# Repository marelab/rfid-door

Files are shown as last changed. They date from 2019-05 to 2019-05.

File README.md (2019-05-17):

marelab rfid-door
# ESP8266 RFID - Access Control with Wiegand Protocol powerd by Door Bell transformer 8-12V AC or DC

## First of all 
big thanks to the [ESP-RFID Project](https://github.com/esprfid/esp-rfid) with the work they have done. The "rfid-door" hardware is 100% compatible with their software also a modified [Firmware](https://github.com/marelab/esp-rfid/releases) with extended MQTT support is included with the marelab RFID-DOOR Version that can be used. Just the hardware design is differnt in my version. The RFID-DOOR pcb is designed to be powered directly from the AC Ring Bell transformer (8-12V AC). But can also be configured to use a 8-12V DC power by just solder bridges. Main reason why I used a different design was the fact that I didn't wanted to setup a new DC source and cables for that device, it can be integrated without any extra power infrastructure. Most german households have a AC Ringbell with 8 or 12V transformer next to the door. 

## RFID-DOOR
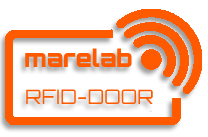
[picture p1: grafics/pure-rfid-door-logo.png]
 
 NFC/RFID WIFI Access Control hardware interfacing a cheap MFRC522, PN532 RFID, RDM6300 readers or Wiegand RFID readers with a Espressif's ESP8266 Microcontroller as Wifi Bridge to drive the door open coil to unlock a home door and to include it into a home automatisation system. The pcb is designed with [KiCad](http://kicad-pcb.org/) an opensoure EDA System. Ready Gerber Files can be found under Gerber. Plz use the Version Tab for download the newest Release the Master Branch includes the current development stage! 

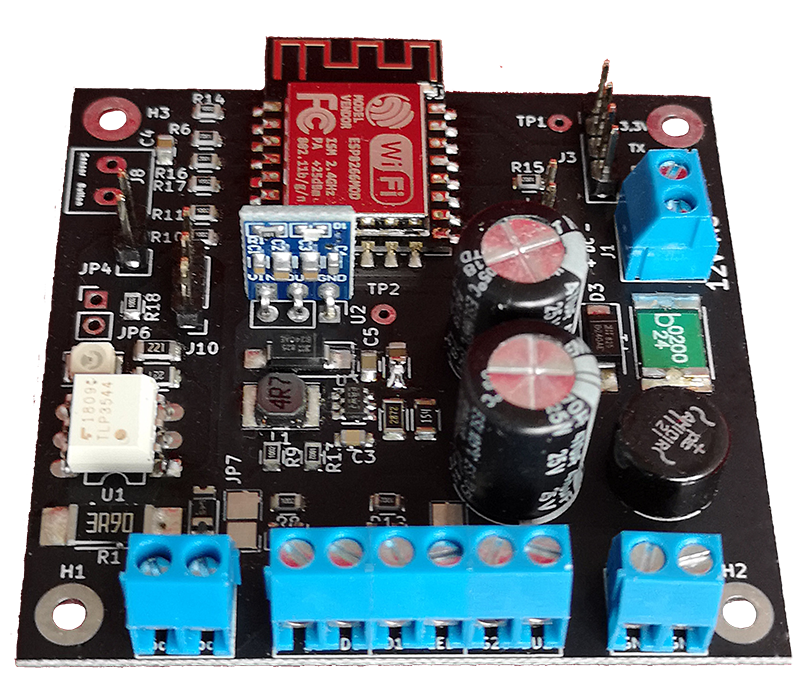
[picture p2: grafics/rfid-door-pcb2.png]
Board
 

## Differnces of the ESP-RFID Hardware to RFID-DOOR Hardware
The marelab RFID-DOOR hardware: 
```
* Can be powered by AC RingBell transformer directly no seperate power source need at the installation spot
* No mechanical Relais just Silicon Door coil is driven by smal opto mosfet
* Currentlimitation of the door coil to limit the current breakdown while magentic lock is activated  
* 5V kompatible Wiegand DO/D1 Lines as default
```

## Features
### For Users
* Minimal effort for setting up your Access Control system, just flash and everything can be configured via Web UI
* Capable of managing up to 1.000 Users (even more is possible)
* Great for Maker Spaces, Labs, Schools, etc
* Cheap to build and easy to maintain
### For Tinkerers
* Open Source (minimum amount of hardcoded variable, this means more freedom)
* Using WebSocket protocol to exchange data between Hardware and Web Browser
* Data is encoded as JSON object
* Records are Timestamped (Time synced from a NTP Server)
* MQTT enabled for using by Smart Home automatisation.
* Bootstrap, jQuery, FooTables for beautiful Web Pages for both Mobile and Desktop Screens
* Thanks to ESPAsyncWebServer Library communication is Asynchronous
### Official Hardware
* Small size form factor just 4,5cm * 4,5 cm
* Single power source (Ring Bell transformer) for RFID-DOOR hardware & RFID Wiegand Reader and magnetic lock for opening doors.
* Exposed programming pins for ESP8266
* Regarding hardware design, you get multiple possible setup options:
* Forward Bell ringing on reader to MCU or pass it out of board
* Control reader’s status LED
* Control reader’s status BUZZER sound *
* Power reader, lock and the board through single 8V, AC Ring Bell Transformer
* Power for Magnetic Lock / Door Relais is supplied by RFID-DOOR Hardware
* Possible to use any kind and any type of Wiegand readers
* Smart Home integration over MQTT
* Fits in an universal enclosures with DIN mount
* Open Source Hardware

## Getting Started
New features (and also bugs) are introduced often and some functions may become deprecated. Please feel free to comment or give feedback.

### Standard Door Bell Setup
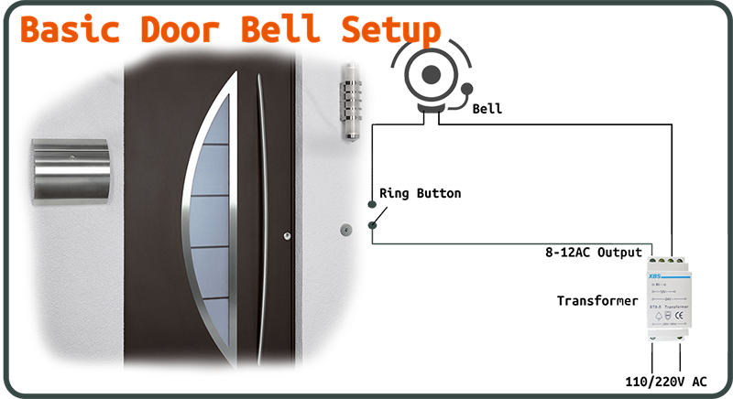
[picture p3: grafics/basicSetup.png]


### RFID-DOOR integrated into Door Bell Setup
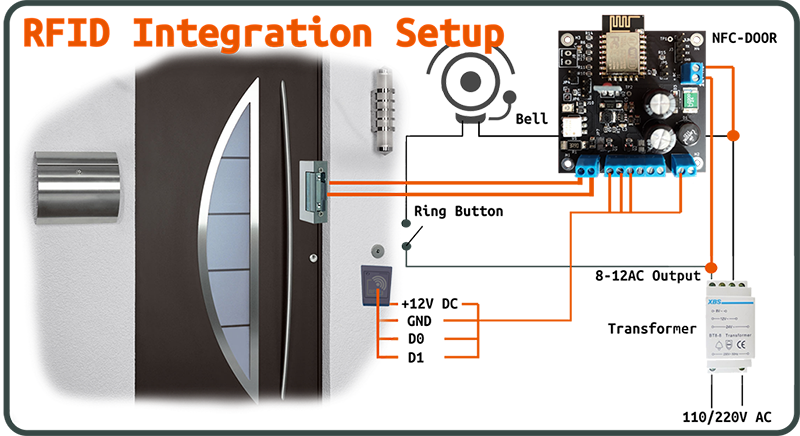
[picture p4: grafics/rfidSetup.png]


## Hardware you need

### Hardware
* [marelab RFID-DOOR Board](https://www.marelab.org/index.php/smarthome-iot/rfid-door) can be ordered here
* A MFRC522 RFID PCD Module or PN532 NFC Reader Module or RDM6300 125KHz RFID Module Wiegand based RFID reader
* n quantity of Mifare Classic 1KB (recommended due to available code base) PICCs (RFID Tags) equivalent to User Number
* A door Relay 8-12V
* A Ringbell Transformer 8-12V 

### Software you need
* Get the latest hardware release from [here.](https://github.com/marelab/rfid-door/releases)
* Get the firmware software from [here.](https://github.com/marelab/esp-rfid/releases)
* See Building [Building](https://github.com/marelab/rfid-door#building)
* See [Security](https://github.com/marelab/esp-rfid#security) for your safety.
* See [ChangeLog](https://github.com/marelab/esp-rfid/blob/dev/CHANGELOG.md)

### Setup & get it running 
* First, flash firmware (you can use /bin/flash.bat on Windows) to your ESP either using Arduino IDE or with your favourite flash tool
* (optional) Fire up your serial monitor to get informed
* Search for Wireless Network "esp-rfid-xxxxxx" and connect to it (It should be an open network and does not require password)
* Open your browser and type either "http://192.168.4.1" or "http://esp-rfid.local" (.local needs Bonjour installed on your computer) on address bar.
* Log on to ESP, default password is "admin"
* Go to "Settings" page
* Configure your amazing access control device. Push "Scan" button to join your wireless network, configure RFID hardware, Relay Module.
* Save settings, when rebooted your ESP will try to join your wireless network.
* Check your new IP address from serial monitor and connect to your ESP again. (You can also connect to "http://esp-rfid.local")
* Go to "Users" page
* Scan a PICC (RFID Tag) then it should glimpse on your Browser's screen.
* Type "User Name" or "Label" for the PICC you scanned.
* Choose "Allow Access" if you want to
* Click "Add"
* Congratulations, everything went well, if you encounter any issue feel free to ask help on GitHub.

### RFID-DOOR Connectors
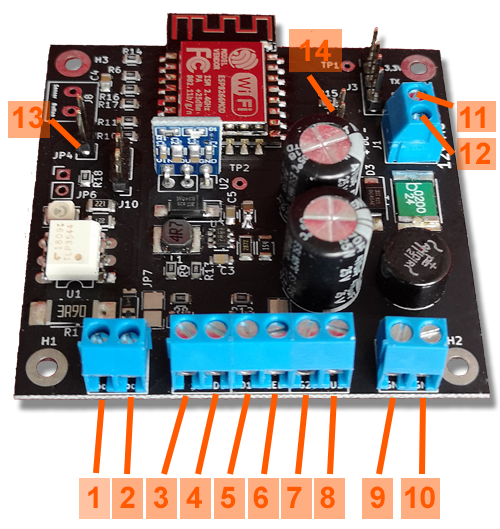
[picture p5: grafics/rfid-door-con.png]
 
 
| Number | Function | ESP8266 |
|---:|:---:|:---|
| 1 | DoorR / Magnetic Look / Door Relais Conector | - |
| 2 | DoorR / Magnetic Look / Door Relais Conector | - |
| 3 | 12V out / 12V+ DC | - |
| 4 | D0 Wiegand D0 | GPIO-04* |
| 5 | D1 Wiegand D1 | GPIO-05*	 |
| 6 | LED | GPIO-05 |
| 7 | W26 | GPIO-05 |
| 8 | BUZ | GPIO-05 |
| 9 | GND | - |
| 10 | GND | - |
| 11 | 12V AC | - |
| 12 | 12V AC | - |
| 13 | JP4 Reset | GPIO-05 |
| 14 | JP5 Firmware Upload enable | GPIO-05 |
| | JP3-1 3,3V Serial Connector to ESP8266 | |
| | JP3-2 TX Serial Connector to ESP8266 | GPIO-05 |
| | JP3-3 RX Serial Connector to ESP8266 | GPIO-05 |
| | JP3-4 GND Serial Connector to ESP8266 | GPIO-05 |

(*) 5V In/Output Signal

### RFID-DOOR Functional Blocks
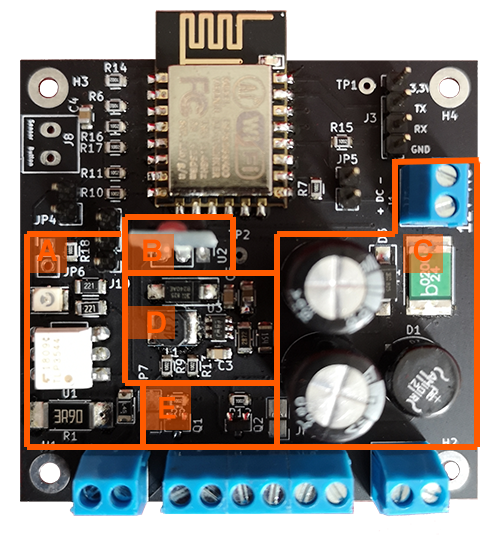
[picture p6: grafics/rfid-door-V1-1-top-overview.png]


| Letter | Hardware Function Block | 
|---:|:---:|
| A | Switches the Magnetic Lock/Door Relais by Opto Mosfet and 2W Magnetic Lock Resistor that limits starting current |
| B | 3,3V Linear Driver for ESP8266 supply | 
| C | Diode Bridge & Self Resetable Fuse for converting AC to DC Ripple power. The Cxx Cap is decoupled by a the Diode Dxx if the 12V of the Bridge falls down for ms while the magnetic lock is used it delivers the energy for the 5V stage  | 
| D | 5V StepDown Converter that powers (B) and the MosFet for (E) | 
| E | In / Out 3,3V Signal Lines ESP to 5V on Conector 

## **Building** & Setup Hardware

#### The AC Ring Bell Transformer
Be carefull with 12V AC Ring bell transformers. The DC Voltage after the Diode bridge can be around 18V DC!!! That will not kill the RFID-DOOR hardware but it will kill a 12V RFID Reader that is connected to the RFID-DOOR. Why is that happening most Readers have a build in AMS1117 Voltage regulator wich has a maximum 16V input. The RFID-DOOR transforms the AC input Voltage in three stages first Stage is a diode bridge to transform AC to rippled DC then a Step Down Regulator generates 5V DC that can handle 24V DC input next the 5V is converted to 3,3V with a AMS1117 for the ESP. The RFID-DOOR won't get killed because the AMS1117 lives behind the 5V StepDown stage. The Rippled DC is connected directly to the power reader connectors. 
The easiest way to get around that problem is using a 8V AC Ringbell transformer. For example someting like this:
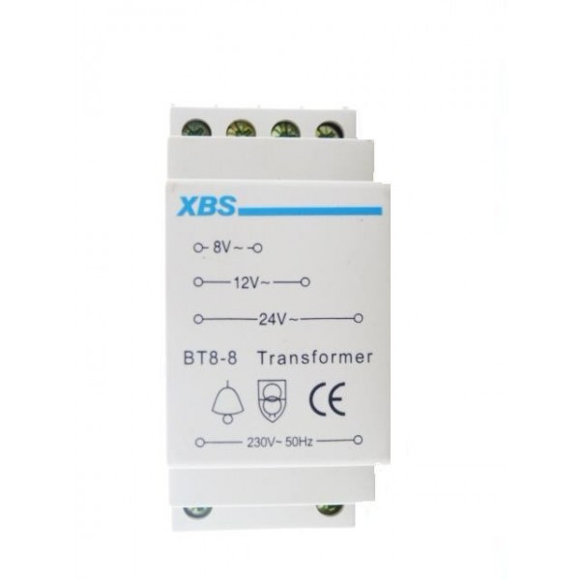
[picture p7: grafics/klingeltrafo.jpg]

Just use the 8V instead of 12V. The rippled DC after the Diode Bridge is around 14-15V and in the range a AMS1117 of the Reader can handle.
Just for details about german standard and regulations for the bell transformer that has to be used. https://de.wikipedia.org/wiki/Klingeltransformator

####  Placing the ACT4088 IC
The ACT4088 Step Down is a quite tiny part and its quite inpossible to indetify Pin1 without a mircoscope or strong lense. As hint thats a picture of the ACT4088 to find Pin1 as marked in the image.
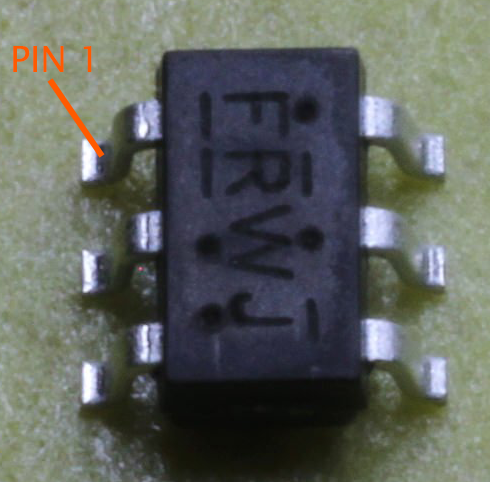
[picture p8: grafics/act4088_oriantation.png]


#### Cad drawing 
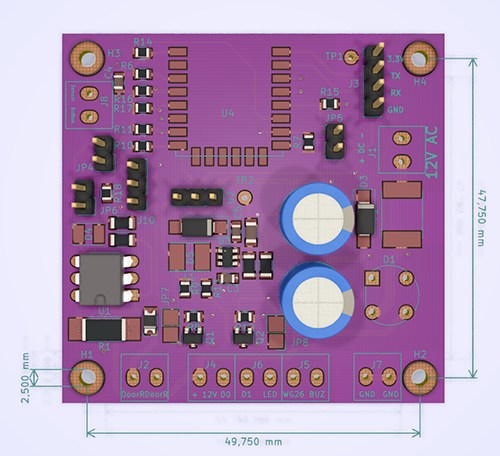
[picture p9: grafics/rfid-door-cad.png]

The Encloser drill holes dimension is 2,5 mm

#### Special Configuration solder bridges
The board can be customized for special needs if you don't want or have a standard configuration. Some solder Bridges see the pictures of the PCB Back & Top where to find them can configure direct 12V DC Input and or disable the 5V Stage for the D0 / D1 pins. 

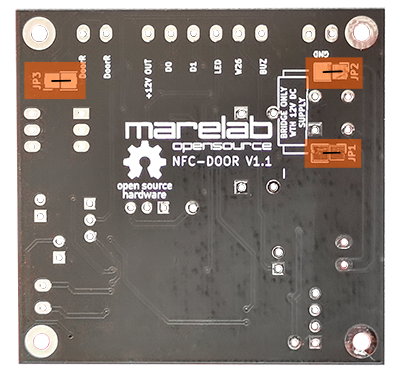
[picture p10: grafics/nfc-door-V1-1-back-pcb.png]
RFID-DOOR back PCB
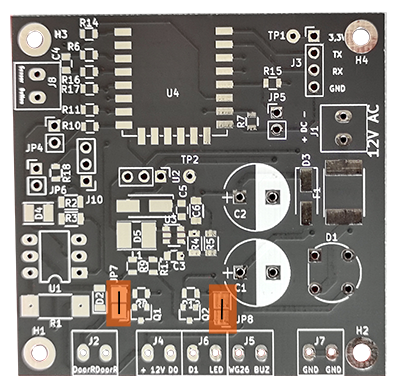
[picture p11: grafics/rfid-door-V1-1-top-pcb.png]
RFID-DOOR top PCB
 

!!!Warning all described here might disable some safety features of the board so you should totaly know what you are doing using this!!!

```
##### 12V DC Power Input
If your power source is 12V DC you don't need the Diode Bridge and the 
Capacitor Cxx to be soldered on the board. Solder the JP1 and JP2 
Solder Bridge Jumpers  
```

```
##### 3,3V DO / D1 Wiegand Interface
If you don't need a 5V TTL compatble In/Out of the D1/D0 Lines just 
solder the Solder Bridges JP7/JP8. Don't solder then the Mosfets Q1 & 
Q2 as well as the four Resistors Rxx,Rxx,Rxx,Rxx. 
```

```
##### Bridge the Magnetic Lock / Door Relais current limitation 
By solder the JP3 Bridge the R1 2W Resistor is bridged and so no current 
limitation of a starting magentic coil / Door Lock saves the MosFet!!! 
The R1 Resitor don't need to be solderd anymore. 
```

## Software

#### Wich firmware should I use?
If you want to have a smart home integration or want to manage more then one Door I would recomend the marelab version, because of the extended MQTT functions and multi device support.
Otherwise you can use also the orginal firmware from the ESP-RFID Project. 

#### Using Compiled Binaries
Download compiled binaries from GitHub Releases page:
marelab modified firmware with extended MQTT support https://github.com/marelab/esp-rfid/releases 
or the orignal firmware from https://github.com/esprfid/esp-rfid/releases

#### Flashing the device
For a selfmade NF-DOOR pcb you need a USB to serial Bridge to flash the first Version. New Firmware Versions can then be updated by OTA (Over the Air Wifi Update) done with the web gui.
If you bought the RFID-DOOR Hardware the ESP is already programmed with the firmware so you don't need the USB to serial adapter for flashing.
On Windows you can use **"flash.bat"**, it will ask you which COM port that ESP is connected and then flashes it. You can use any flashing tool and do the flashing manually. The flashing process itself has been described at numerous places on Internet.

#### Self building With PlatformIO
##### Backend
The build environment is based on [PlatformIO](http://platformio.org). Follow the instructions found here: http://platformio.org/#!/get-started for installing it but skip the ```platform init``` step as this has already been done, modified and it is included in this repository. In summary:

```
sudo pip install -U pip setuptools
sudo pip install -U platformio
git clone https://github.com/esprfid/esp-rfid.git
cd esp-rfid
platformio run
```

When you run ```platformio run``` for the first time, it will download the toolchains and all necessary libraries automatically.

##### Debug information
When you compiling and flashing a debug Version the ESP sends Debug Messages over the Serial Port thats usefull for trace and test purpose.

##### Useful commands:

* ```platformio run``` - process/build all targets
* ```platformio run -e generic -t upload``` - process/build and flash just the ESP12e target 
* ```platformio run -e debug -t upload``` - process/build and flash just the ESP12e target 
* ```platformio run -t clean``` - clean project (remove compiled files)

The resulting (built) image(s) can be found in the directory ```/bin``` created during the build process.

##### Frontend
You can not simply edit Web UI files because you will need to convert them to C arrays, which can be done automatically by a gulp script that can be found in tools directory or you can use compiled executables at the same directory as well (for Windows PCs only).

If you want to edit esp-rfid's Web UI you will need (unless using compiled executables):
* NodeJS
* npm (comes with NodeJS installer)
* Gulp (can be installed with npm)

Gulp script also minifies HTML and JS files and compresses (gzip) them. 

In order to test your changes without flashing the firmware you can launch websocket emulator which is included in tools directory.
* You will need to Node JS for websocket emulator.
* Run ```npm update``` to install dependencies
* Run emulator  ```node wserver.js```
* then you will need to launch your browser with CORS disabled:
* ```chrome.exe --args --disable-web-security -–allow-file-access-from-files --user-data-dir="C:\Users\USERNAME"```

Get more information here: https://stackoverflow.com/questions/3102819/disable-same-origin-policy-in-chrome

### Pin Layout

The following table shows the typical pin layout used for connecting readers hardware to ESP:

| ESP8266 | NodeMcu/WeMos | Wiegand | PN532 | MFRC522 | RDM6300 | 
|---:|:---:|:---:|:-----:|:---:|:---:|
| GPIO-15 | D8 | | SS | SDA/SS  | |
| GPIO-13 | D7 | D0 | MOSI  | MOSI | |
| GPIO-12 | D6 | D1 | MISO  | MISO | |
| GPIO-14 | D5 | | SCK | SCK | TX |
| GPIO-04 | D2 | | | | |
| GPIO-05 | D1 | | | | |

For Wiegand based readers, you can configure D0 and D1 pins via settings page. By default, D0 is GPIO-4 and D1 is GPIO-5

## Time
We are syncing time from a NTP Server (in Client -aka infrastructure- Mode). This will require ESP to have an Internet connection. Additionally your ESP can also work without Internet connection too (Access Point -aka Ad-Hoc- Mode),  without giving up functionality.
This will require you to do syncing manually. ESP can store and hold time for you approximately 51 days without a major issue, device time can drift from actual time depending on usage, temperature, etc.
So you have to login to settings page and sync it in a timely fashion.

## **Security**
We assume **ESP-RFID** project -as a whole- does not offer strong security. There are PICCs available that their UID (Unique Identification Numbers) can be set manually (Currently esp-rfid relies only UID to identify its users). Also there may be a bug in the code that may result free access to your belongings. And also, like every other network connected device esp-rfid is vulnerable to many attacks including Man-in-the-middle, Brute-force, etc.

This is a simple, hobby grade project, do not use it where strong security is needed.

What can be done to increase security? (by you and by us)

* We are working on more secure ways to Authenticate RFID Tags.
* You can disable wireless network to reduce attack surface. (This can be configured in Web UI Settings page)
* Choose a strong password for the Web UI

## Scalability
Since we are limited on both flash and ram size things may get ugly at some point in the future. You can find out some test results below.

## License
The code parts are licensed under [MIT License](https://github.com/esprfid/esp-rfid/blob/stable/LICENSE), 3rd party libraries that are used by this project are licensed under different license schemes, please check them out as well.

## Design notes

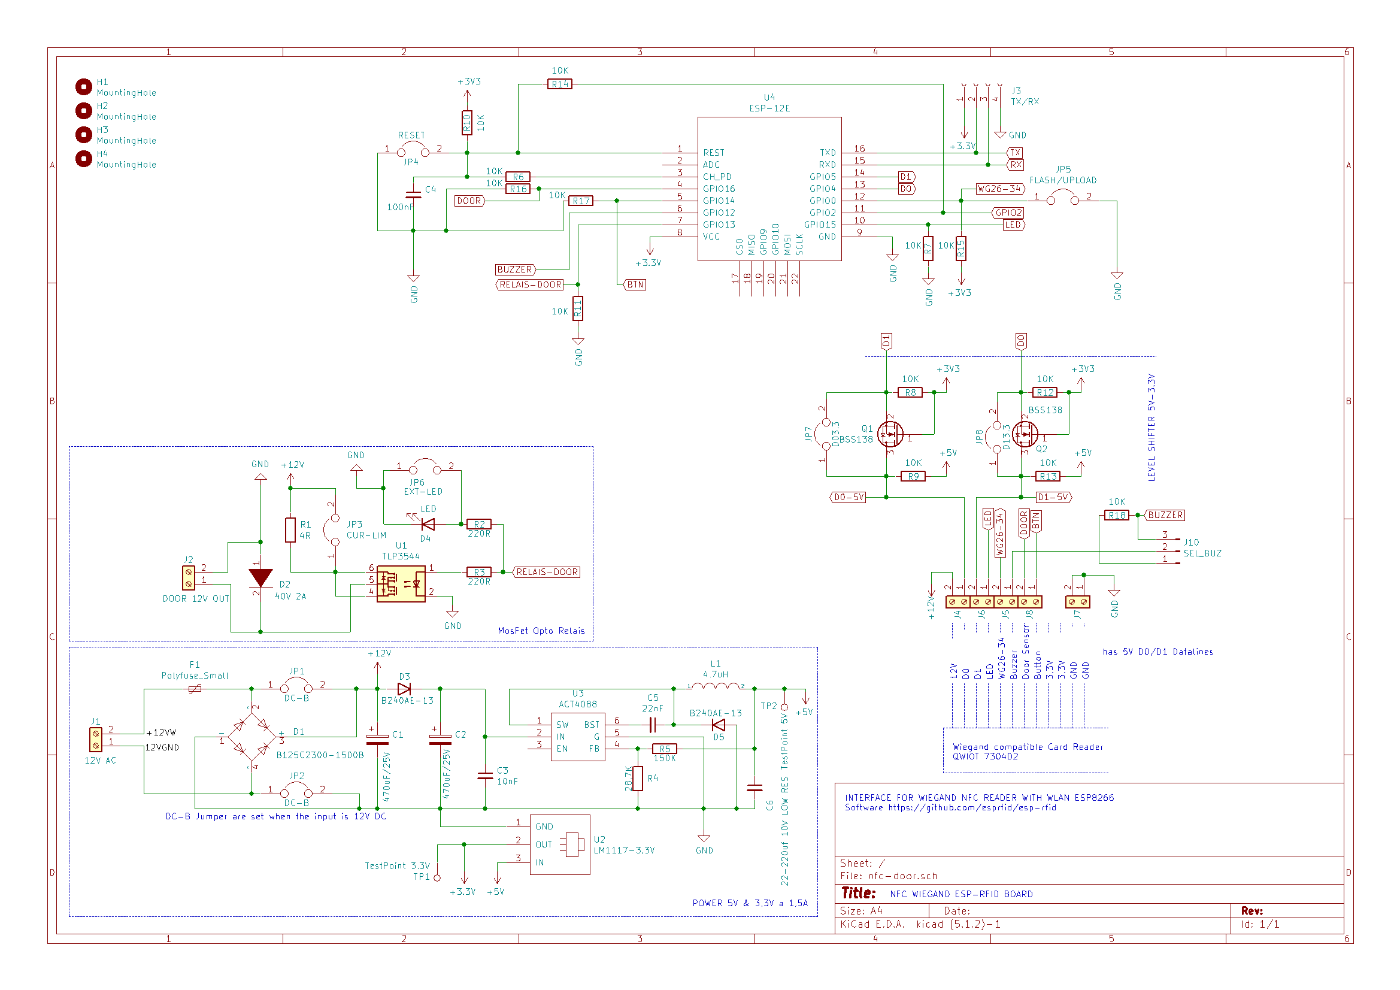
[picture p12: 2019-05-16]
grafics/schematic-rfid-door-v1-1.png

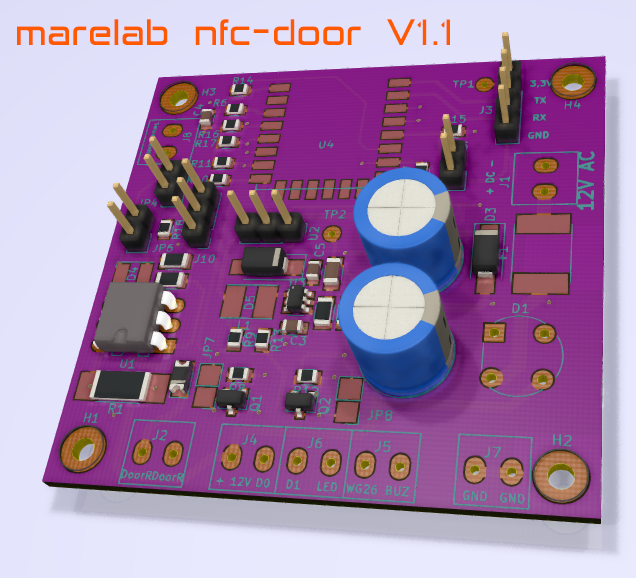
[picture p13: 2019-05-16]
grafics/rfid-door-V-1-1-3D.png

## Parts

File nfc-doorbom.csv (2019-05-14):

Pos | Description | Part | Name | Wert | Footprint | Quantity Per PCB | Datasheet | manf-num
1 |  | C_Small | C4 | 100nF | C_0805 | 1 | https://www.mouser.de/ProductDetail/Murata-Electronics/GCM21BR70J106KE22L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 | CC0805KPX7R8BB104
2 |  | C_Small | C3 | 10nF | C_0805 | 1 |  | CC0805KRX7R8BB103
3 |  | C_Small | C6 | 22-220uf 10V LOW RES | C_1206 | 1 |  | CC0805JRX7R8BB223
4 |  | C_Small | C5 | 22nF | C_0805 | 1 |  | CC0805JRX7R8BB223
5 | Polarized capacitor | CP | C1 C2 | 470uF/25V | CP_Radial_D10.0mm_P5.00mm | 2 | https://www.mouser.de/datasheet/2/212/KEM_A4074_ESL-1128319.pdf | ESL477M025AH9
6 | Diode symbol for simulation only. Pin order incompatible with official kicad footprints | DIODE | D2 | 40V 2A | D_1206 | 1 | https://www.mouser.de/ProductDetail/AVX/SD1206T040S2R0 | SD1206T040S2R0
7 | Silicon Bridge Rectifier, 125V Vrms, 1.5A If, pins=-A+A, SIL-package | B125C2300-1500B | D1 | B125C2300-1500B | Diode_Bridge_Round_D8.9mm | 1 | https://diotec.com/tl_files/diotec/files/pdf/datasheets/b40c2300.pdf
8 | Diode | D | D3 D5 | B240AE-13 | D_SMA_Handsoldering | 2 | https://www.mouser.de/datasheet/2/115/B220AEBE-B245AEBE-1115122.pdf | B240AE-13
9 | Light emitting diode | LED | D4 | LED | LED_0805 | 1 | ~
10 | Resettable fuse, polymeric positive temperature coefficient, small symbol | Polyfuse_Small | F1 | Polyfuse_Small | Fuse_SMD2920 | 1 | https://www.mouser.de/ProductDetail/Bel-Fuse/0ZCF0200AF2C | 0ZCF0200AF2C
11 | Generic screw terminal, single row, 01x02 | Screw_Terminal_01x02 | J4 J5 J6 J7 J8 |  | RM3.5-CON | 5 | ~
12 | Generic screw terminal, single row, 01x02 | Screw_Terminal_01x02 | J1 | 12V AC | RM3.5-CON | 1 | ~
13 | Generic screw terminal, single row, 01x02 | Screw_Terminal_01x02 | J2 | DOOR 12V OUT | RM3.5-CON | 1 | ~
14 | Generic connector, single row, 01x03, script generated (kicad-library-utils/schlib/autogen/connector/) | Conn_01x03_Male | J10 | SEL_BUZ | Pin_Header_Straight_1x03_Pitch2.54mm | 1 | ~
15 | Generic connector, single row, 01x04, script generated (kicad-library-utils/schlib/autogen/connector/) | Conn_01x04_Female | J3 | TX/RX | Pin_Header_Straight_1x04_Pitch2.54mm | 1 | ~
16 | Jumper, normally closed | Jumper | JP3 | CUR-LIM | SolderBridge | 1 | ~
17 | Jumper, normally closed | Jumper | JP7 | D03,3 | SolderBridge | 1 | ~
18 | Jumper, normally closed | Jumper | JP8 | D13,3 | SolderBridge | 1 | ~
19 | Jumper, normally closed | Jumper | JP1 JP2 | DC-B | SolderBridge | 2 | ~
20 | Jumper, normally closed | Jumper | JP6 | EXT-LED | Pin_Header_Straight_1x02_Pitch2.54mm | 1 | ~
21 | Jumper, normally closed | Jumper | JP5 | FLASH/UPLOAD | Pin_Header_Straight_1x02_Pitch2.54mm | 1 | ~
22 | Jumper, normally closed | Jumper | JP4 | RESET | Pin_Header_Straight_1x02_Pitch2.54mm | 1 | ~
23 | Capacitor symbol for simulation only | INDUCTOR | L1 | 4,7uH | Inductor_Taiyo-Yuden_NR-40xx_HandSoldering | 1 | SRN4026-4R7M | SRN4026-4R7M
24 | 50V Vds, 0.22A Id, N-channel MOSFET, SOT-23 | BSS138 | Q1 Q2 | BSS138 | SOT-23 | 2 | https://www.fairchildsemi.com/datasheets/BS/BSS138.pdf | BSS138
25 |  | R | R6 R7 R8 R9 R10 R11 R12 R13 R14 R15 R16 R17 R18 | 10K | R_0805 | 13
26 |  | R | R5 | 150K | R_1206 | 1
27 |  | R | R2 R3 | 220R | R_1206 | 2
28 |  | R | R4 | 28,7K | R_1206 | 1
29 |  | R | R1 | 4R | R_2512_HandSoldering | 1 | https://www.mouser.de/ProductDetail/TE-Connectivity-Neohm/CRGH2512J3R3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
30 | 5V StepDown Wandler | ACT4088 | U3 | ACT4088 | SOT-23-6 | 1 |  | ACT4088US-T
31 | ESP8266 ESP-12E module, 22 pins, 2mm, PCB antenna | ESP-12E | U4 | ESP-12E | ESP-12E_SMD | 1 | http://l0l.org.uk/2014/12/esp8266-modules-hardware-guide-gotta-catch-em-all/
32 | 3,3V 1.5A CHINA MODUL | LM1117-3,3V | U2 | LM1117-3,3V | Pin_Header_Straight_1x03_Pitch2.54mm | 1
33 | Photo MOSFET optically coupled, ON 3.5A, 60mohm, OFF state 40V, Isolation 2500 VRMS, DIP-6 | TLP3544 | U1 | TLP3544 | DIP-6_W7.62mm_LongPads | 1 | https://toshiba.semicon-storage.com/info/docget.jsp?did=12661&prodName=TLP3544 | TLP3544(F)

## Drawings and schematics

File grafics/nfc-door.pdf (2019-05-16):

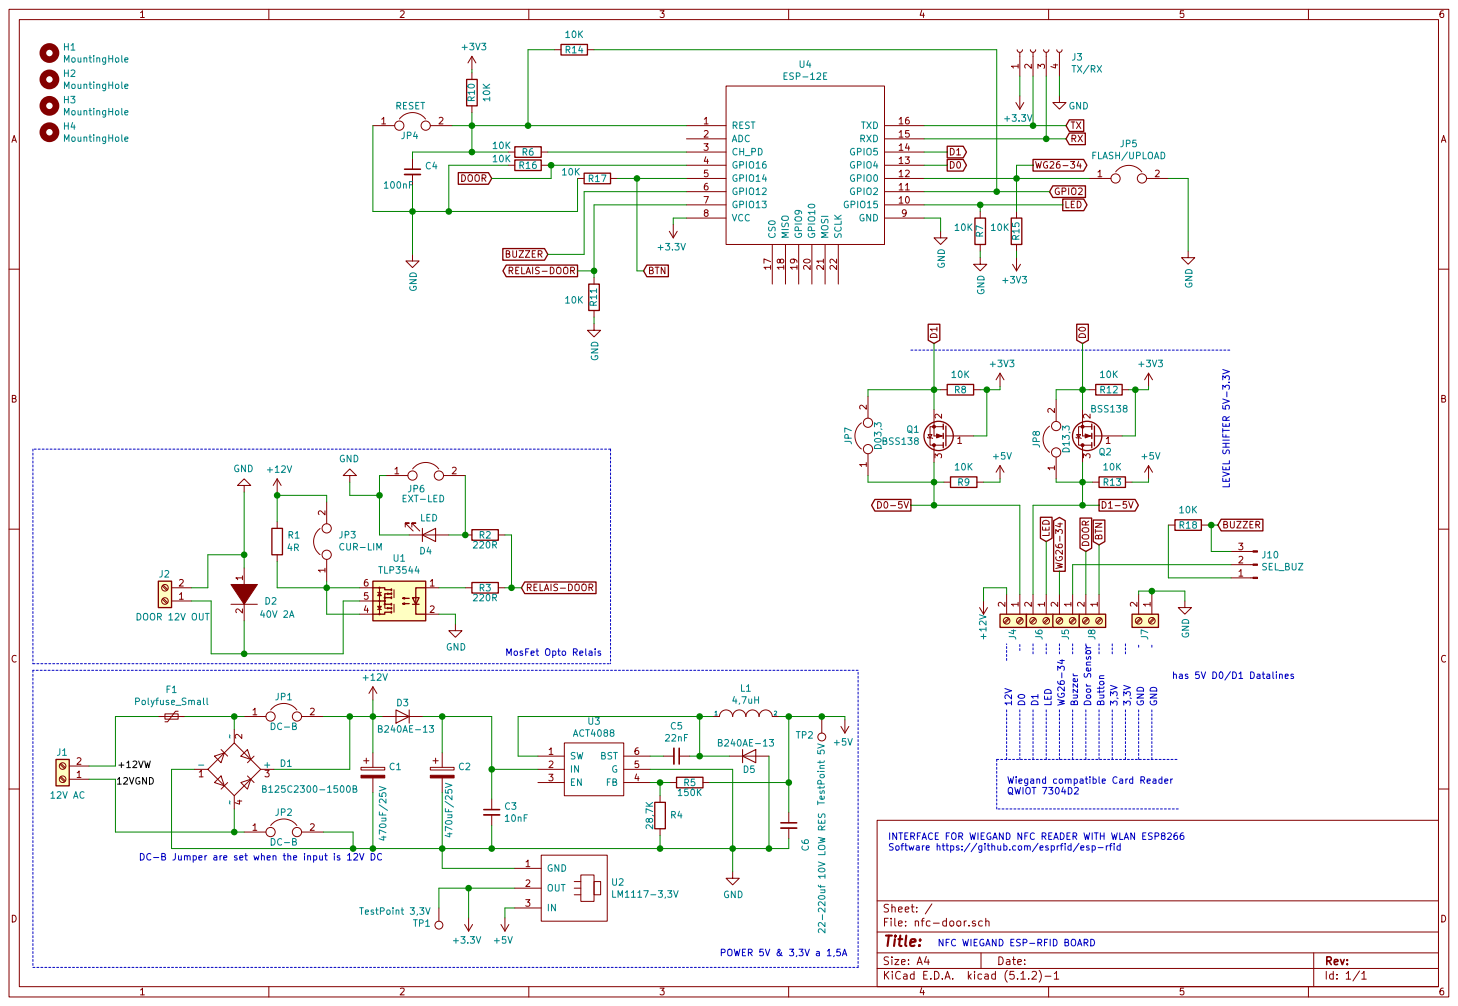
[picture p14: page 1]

J3TX/RX LED WG26-34 Buzzer Door Sensor Button 3,3V 3,3V GND GND
has 5V D0/D1 Datalines R8

JP2 DC-B DC-B Jumper are set when the input is 12V DC

INTERFACE FOR WIEGAND NFC READER WITH WLAN ESP8266 Software https://github.com/esprfid/esp-rfid

Id: 1/1 Title: File: nfc-door.sch Sheet: /

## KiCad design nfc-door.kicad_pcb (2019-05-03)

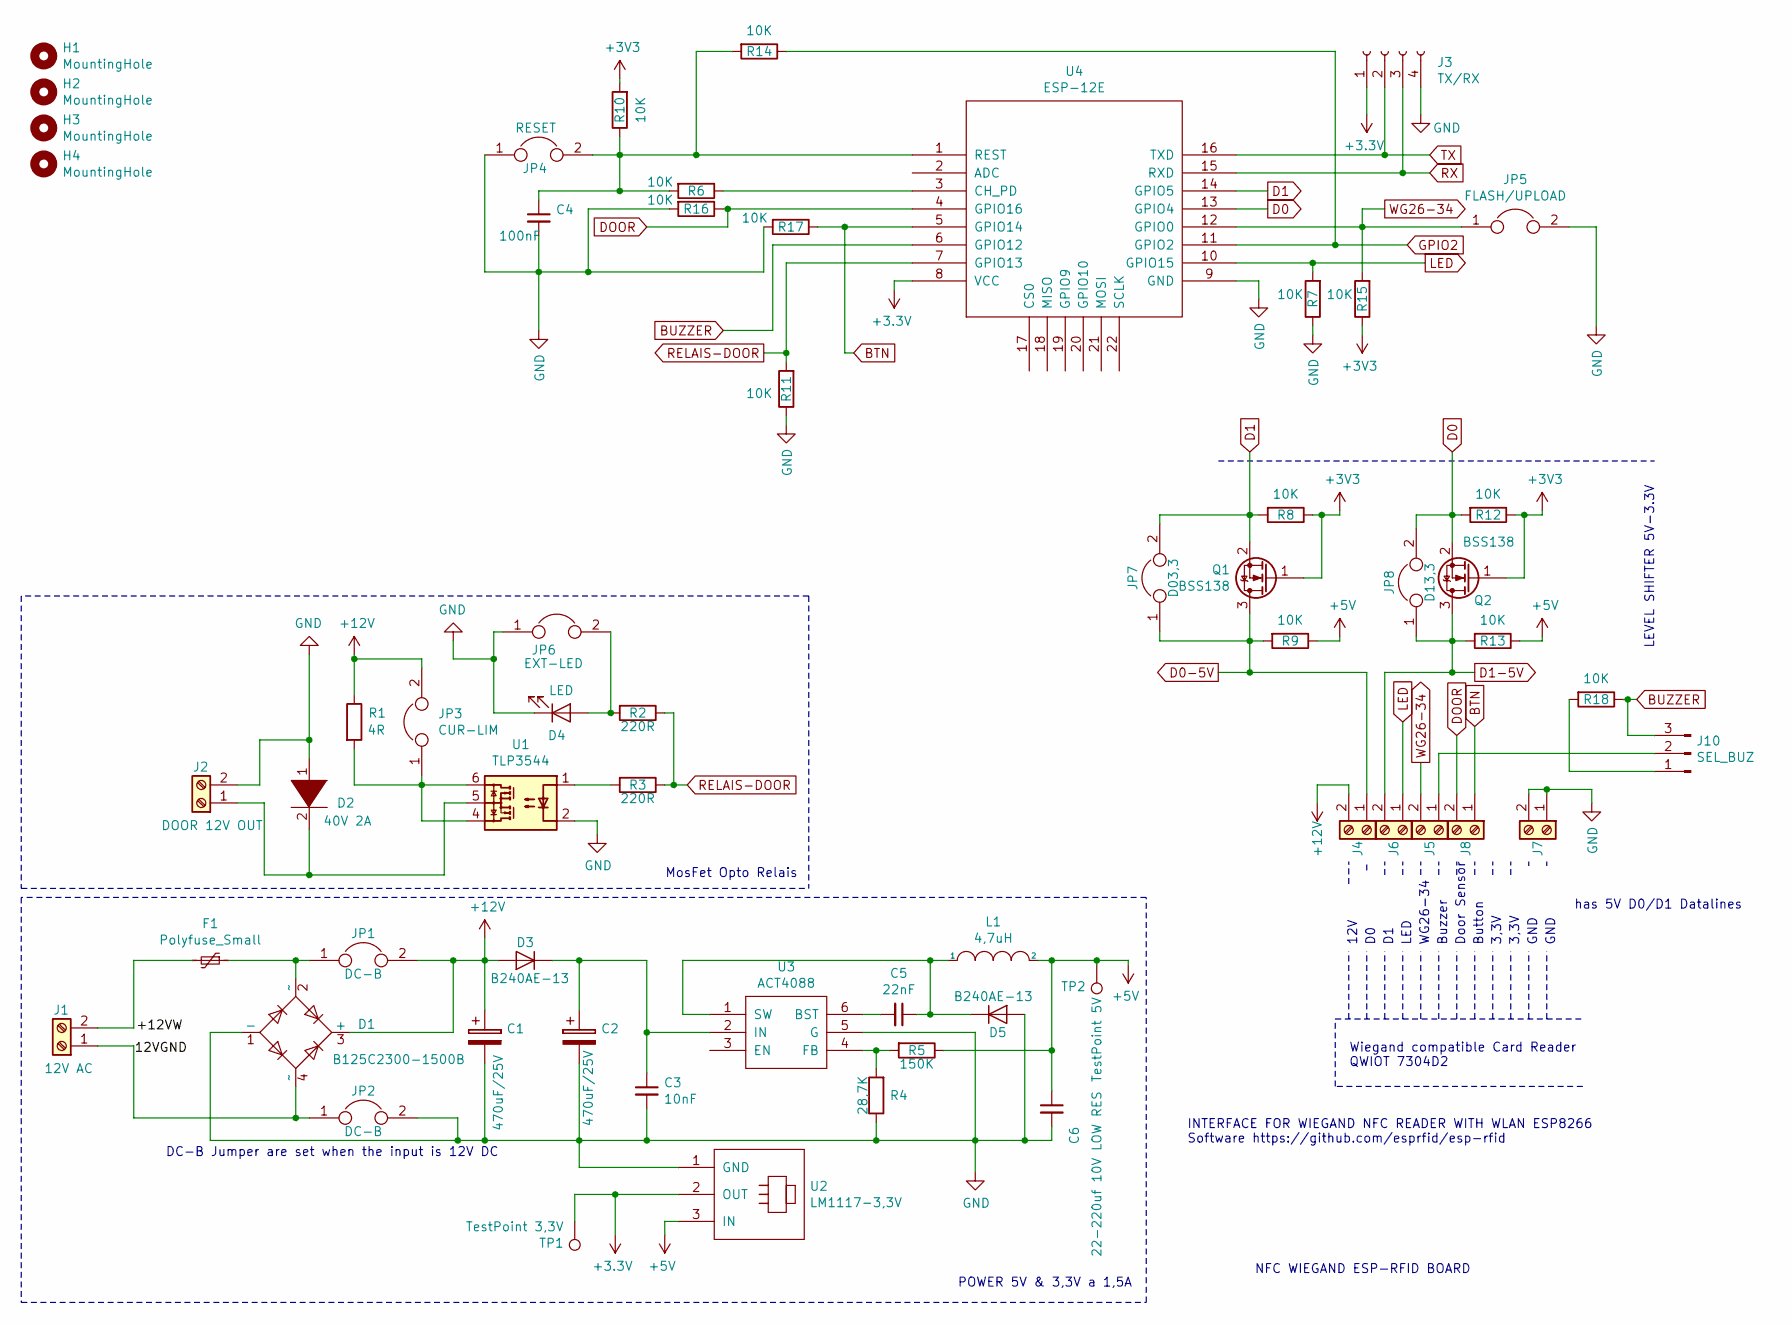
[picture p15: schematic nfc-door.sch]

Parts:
C1, C2: 470uF/25V; CP_Radial_D10.0mm_P5.00mm
C3: 10nF; C_0805
C4: 100nF; C_0805
C5: 22nF; C_0805
C6: 22-220uf 10V LOW RES; C_1206
D1: B125C2300-1500B; Diode_Bridge_Round_D8.9mm
D2: 40V 2A; D_1206
D3, D5: B240AE-13; D_SMA_Handsoldering
D4: LED; LED_0805
F1: Polyfuse_Small; Fuse_SMD2920
H1, H2, H3, H4: MountingHole; MountingHole_2.5mm_Pad
J1: 12V AC; RM3.5-CON
J2: DOOR 12V OUT; RM3.5-CON
J3: TX/RX; Pin_Header_Straight_1x04_Pitch2.54mm
J4, J5, J6, J7, J8: RM3.5-CON
J10: SEL_BUZ; Pin_Header_Straight_1x03_Pitch2.54mm
JP1, JP2: DC-B; SolderBridge
JP3: CUR-LIM; SolderBridge
JP4: RESET; Pin_Header_Straight_1x02_Pitch2.54mm
JP5: FLASH/UPLOAD; Pin_Header_Straight_1x02_Pitch2.54mm
JP6: EXT-LED; Pin_Header_Straight_1x02_Pitch2.54mm
JP7: D03,3; SolderBridge
JP8: D13,3; SolderBridge
L1: 4,7uH; Inductor_Taiyo-Yuden_NR-40xx_HandSoldering
Q1, Q2: BSS138; SOT-23
R1: 4R; R_2512_HandSoldering
R2, R3: 220R; R_1206
R4: 28,7K; R_1206
R5: 150K; R_1206
R6, R7, R8, R9, R10, R11, R12, R13, R14, R15, R16, R17, R18: 10K; R_1206
TP1: TestPoint 3,3V; SolderWirePad_single_0-8mmDrill
TP2: TestPoint 5V; SolderWirePad_single_0-8mmDrill
U1: TLP3544; DIP-6_W7.62mm_LongPads
U2: LM1117-3,3V; Pin_Header_Straight_1x03_Pitch2.54mm
U3: ACT4088; SOT-23-6
U4: ESP-12E; ESP-12E_SMD

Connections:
+5V: C6.1, L1.2, R5.1, R9.1, R13.1, TP2.1, U2.3 (IN)
+12V: C1.1, D1.3 (+), D3.2 (A), J4.2, JP1.2, JP3.2, R1.1
BTN: J8.1, R17.1, U4.5 (GPIO14)
BUZZER: J10.3, R18.1, U4.6 (GPIO12)
D0: JP8.2, Q2.2 (S), R12.2, U4.13 (GPIO4)
D0-5V: J4.1, JP7.1, Q1.3 (D), R9.2
D1: JP7.2, Q1.2 (S), R8.2, U4.14 (GPIO5)
D1-5V: J6.2, JP8.1, Q2.3 (D), R13.2
DOOR: J8.2, R16.1, U4.4 (GPIO16)
GND: C1.2, C2.2, C3.2, C4.2, C6.2, D1.1 (-), D2.1 (K), D4.1 (K), D5.2 (A), J2.2, J3.4, J7.1, J7.2, JP2.2, JP4.1, JP5.2, JP6.1, R4.1, R7.1, R11.1, R16.2, R17.2, U1.2, U2.1 (GND), U3.5 (G), U4.9 (GND)
GPIO2: R14.1, U4.11 (GPIO2)
LED: J6.1, R7.2, U4.10 (GPIO15)
unnamed: C2.1, C3.1, D3.1 (K), U3.2 (IN)
unnamed: C4.1, JP4.2, R6.2, R10.1, R14.2, U4.1 (REST)
unnamed: C5.1, D5.1 (K), L1.1, U3.1 (SW)
unnamed: C5.2, U3.6 (BST)
unnamed: D1.2 (~~), F1.1, JP1.1
unnamed: D1.4 (~~), J1.1, JP2.1
unnamed: D2.2 (A), J2.1, U1.5
unnamed: D4.2 (A), JP6.2, R2.2
unnamed: F1.2, J1.2
unnamed: J10.1, R18.2
unnamed: J5.1, J10.2
unnamed: JP3.1, R1.2, U1.4, U1.6
unnamed: R3.2, U1.1
unnamed: R4.2, R5.2, U3.4 (FB)
unnamed: R6.1, U4.3 (CH_PD)
RELAIS-DOOR: R2.1, R3.1, R11.2, U4.7 (GPIO13)
RX: J3.3, U4.15 (RXD)
TX: J3.2, U4.16 (TXD)
WG26-34: J5.2, JP5.1, R15.2, U4.12 (GPIO0)

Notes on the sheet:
Wiegand compatible Card Reader QWIOT 7304D2
GND
12V
has 5V D0/D1 Datalines
LEVEL SHIFTER 5V-3.3V
NFC WIEGAND ESP-RFID BOARD
INTERFACE FOR WIEGAND NFC READER WITH WLAN ESP8266 Software https://github.com/esprfid/esp-rfid
DC-B Jumper are set when the input is 12V DC
POWER 5V & 3,3V a 1,5A
MosFet Opto Relais
LED
WG26-34
Buzzer
Door Sensor
Button
3,3V
GND

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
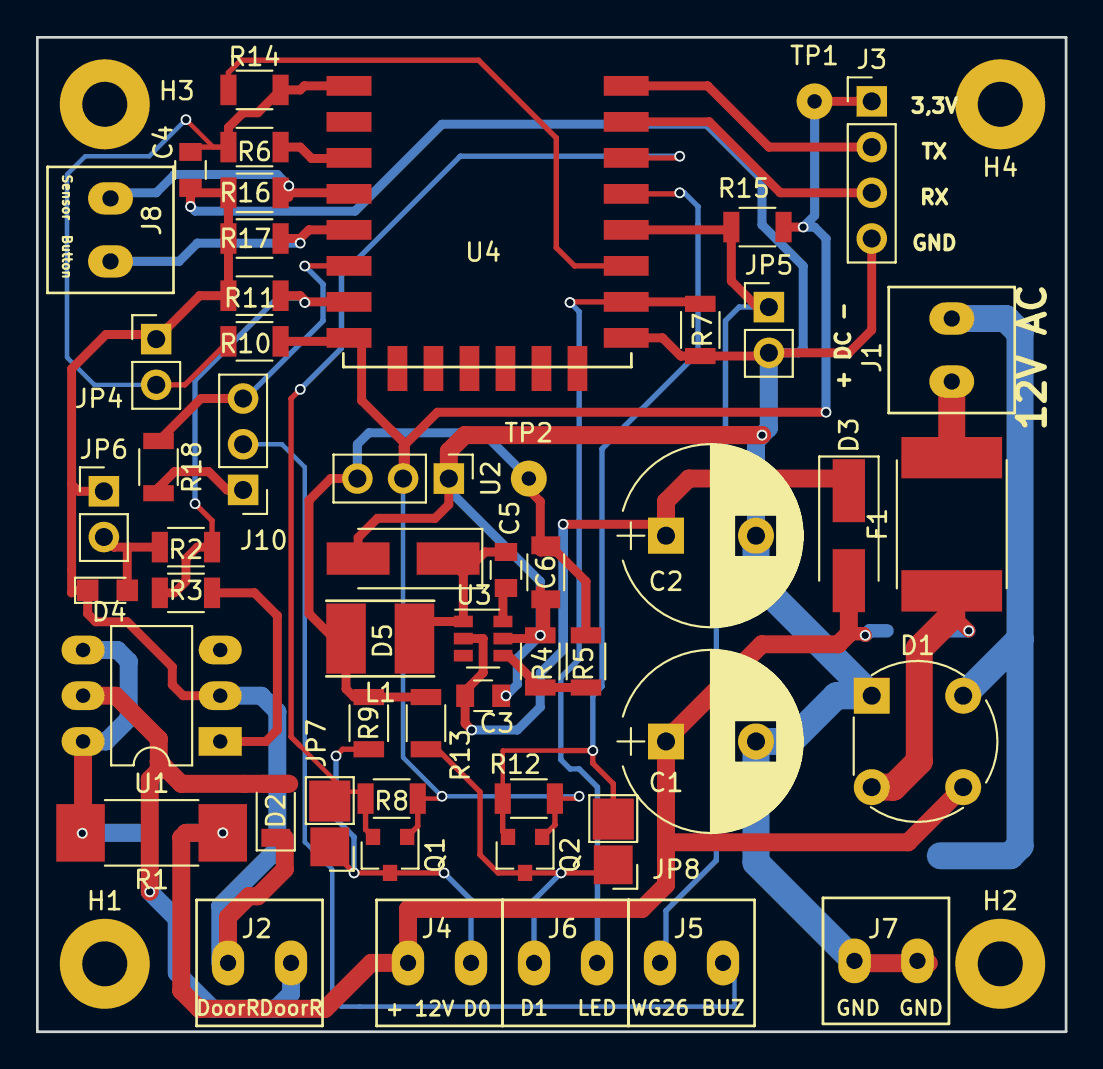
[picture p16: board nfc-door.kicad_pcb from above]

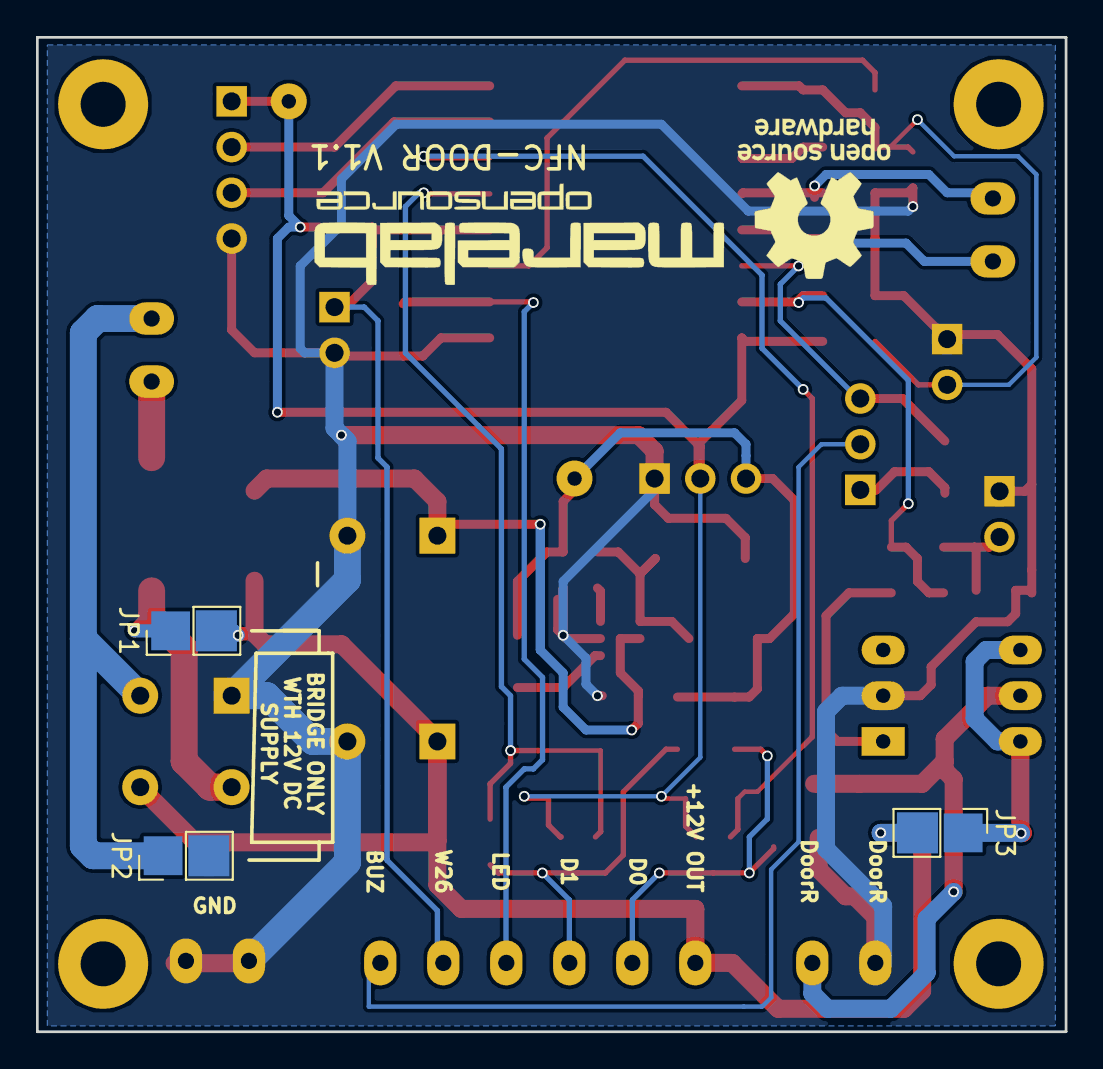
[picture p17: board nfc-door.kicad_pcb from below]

Board: 2 copper layers, 57.2 x 55.2 mm, 60 parts (3 on the bottom side), 32 nets.

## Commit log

2019-05-03 Initial V1.1 Version
    [3-3V-2019-03-08-12-14-50.sch, 3-3V-2019-03-08-12-15-37.sch, cadplexinfx.dxf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]
2019-05-14 V1.1 Version
    Version V1.1
    * Corrected Diode Bridge
    * 1206 22uF CAP
    [nfc-door-B_Cu.gbr, nfc-door-B_Mask.gbr, nfc-door-B_SilkS.gbr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]
2019-05-16 Update Cleaned up Repro
    [nfc-door.csv, nfc-doorbom.csv, nfc-doorbom2.csv]
2019-05-16 Schematic & 3D png/pdf
2019-05-16 Added pcb pic
2019-05-17 Update and grafics Connectors & Overview
2019-05-17 Added Connector Table
2019-05-17 Added Top & Back PCB images
2019-05-17 Special Configuration over Solder Bridges
